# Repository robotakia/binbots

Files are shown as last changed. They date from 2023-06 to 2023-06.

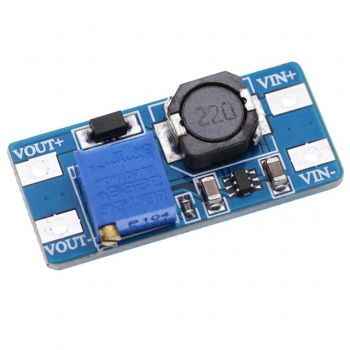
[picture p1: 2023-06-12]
Εξαρτήματα/Μετατροπέας DC-DC Step-Up 5-28V 2A - MT3608.jpg

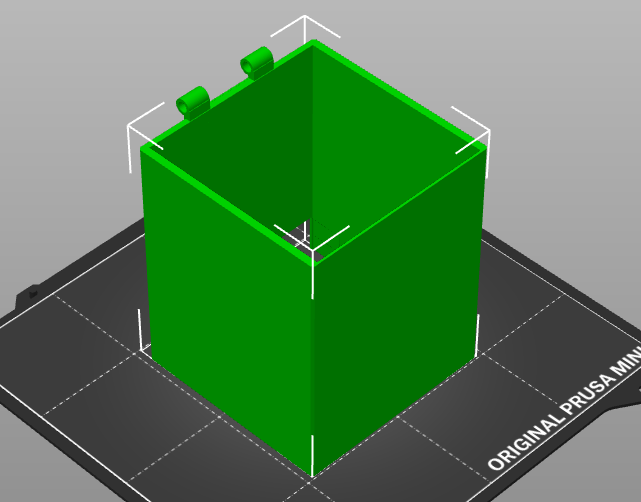
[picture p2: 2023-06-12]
3d printing/main_body.png

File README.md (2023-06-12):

Robotakia Binbots - Έξυπνο σύστημα διαχείρισης απορριμμάτων

5ος Πανελλήνιος Διαγωνισμός Ανοιχτών Τεχνολογιών στην Εκπαίδευση (2023)

Η ομάδα μας υλοποίησε μία μακέτα που αποτελείται από 2 έξυπνους κάδους ανακύκλωσης. Ο κάθε κάδος αντιστοιχεί σε ένα διαφορετικό ανακυκλώσιμο υλικό (π.χ. πλαστικό, χαρτί) και ενεργοποιείται αυτόματα μόλις κλείσει το καπάκι του. Στη συνέχεια ο κάθε κάδος ακολουθεί μία διαφορετική πορεία χωρίς καμία ανθρώπινη παρέμβαση ακολουθώντας τις αντίστοιχες χρωματιστές γραμμές. Επιπλέον, οι κάδοι αδειάζουν τα ανακυκλώσιμα υλικά σε διαφορετικά σημεία και με αυτόν τον τρόπο παρακάμπτεται το στάδιο της διαλογής των ανακυκλώσιμων υλικών.

Η ιστοσελίδα του έργου: https://openedtech.ellak.gr/robotics2023/robotakia-binbots/

Βίντεο παρουσίασης του έργου: https://youtu.be/iRQ4jEklhuc

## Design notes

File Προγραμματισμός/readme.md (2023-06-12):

Για τον προγραμματισμό του Pico με τη CirquitPython συνδέουμε το Pico με ένα καλώδιο usb στον υπολογιστή έχοντας πατημένο το κουμπί bootsel. Στη συνέχεια ρίχνουμε στον φάκελο του Pico το αρχείο adafruit-circuitpython-raspberry_pi_pico-en_US-8.0.5.uf2 . Ο φάκελος lib περιλαμβάνει τις απαραίτητες βιβλιοθήκες. Ο κώδικας που εκτελούν τα ρομποτάκια είναι τα αρχεία blue_bin.py και red_bin.py .

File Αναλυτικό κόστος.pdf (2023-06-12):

Εξάρτημα | Κόστος
Ball Caster with Metal Ball 0.4 | 1,2
Battery Holder 1x18650 with Wires | 0,6
Battery Lithium 18650 3.6V 3200mAh | 4,64
2 x DC Motor in Micro Servo Body | 5
Motor Drive Module Mini L298N | 2
Ks0021 keyestudio Collision Sensor | 3
Raspberry Pi Pico | 5,8
RGB Color Sensor with IR filter - TCS34725 | 9,9
Toggle Switch SPDT ON-OFF-ON (3A/250V) | 0,8
2 x Wheel 40x4mm (Hole Diameter 2mm) | 0,8
Μετατροπέας DC-DC Step-Up 5-28V 2A - MT3608 | 1,6
Σύνολο | 35,34

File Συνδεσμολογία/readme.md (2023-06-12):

Η συνδεσμολογία των ηλεκτρονικών εξαρτημάτων των ρομπότ.

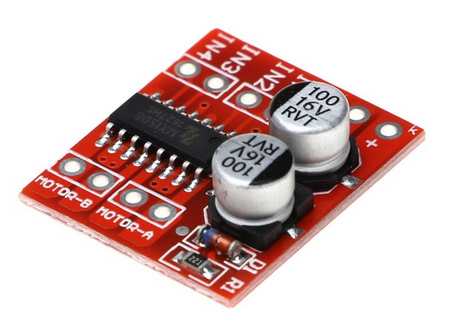
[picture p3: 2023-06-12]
Εξαρτήματα/Motor Drive Module Mini L298N.png

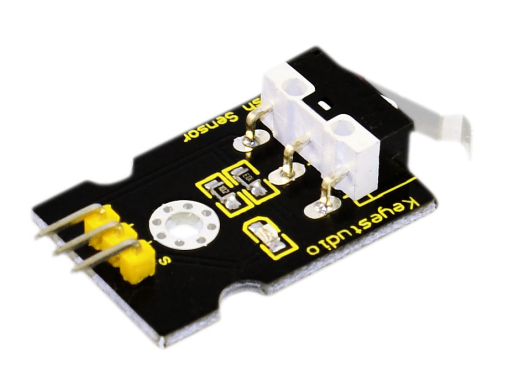
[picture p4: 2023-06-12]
Εξαρτήματα/Ks0021 keyestudio Collision Sensor.png

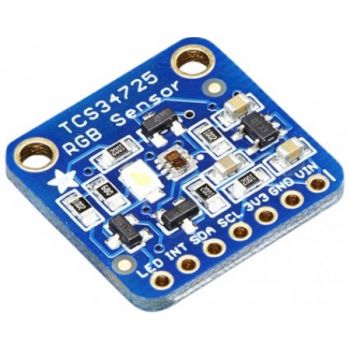
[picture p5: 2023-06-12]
Εξαρτήματα/RGB Color Sensor with IR filter - TCS34725.jpg

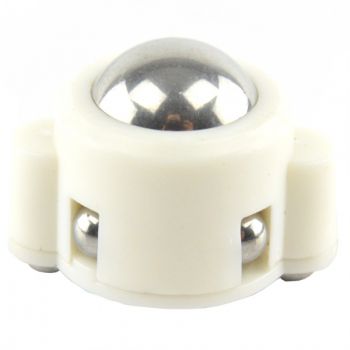
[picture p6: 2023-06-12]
Εξαρτήματα/Ball Caster with Metal Ball 0.4.jpg

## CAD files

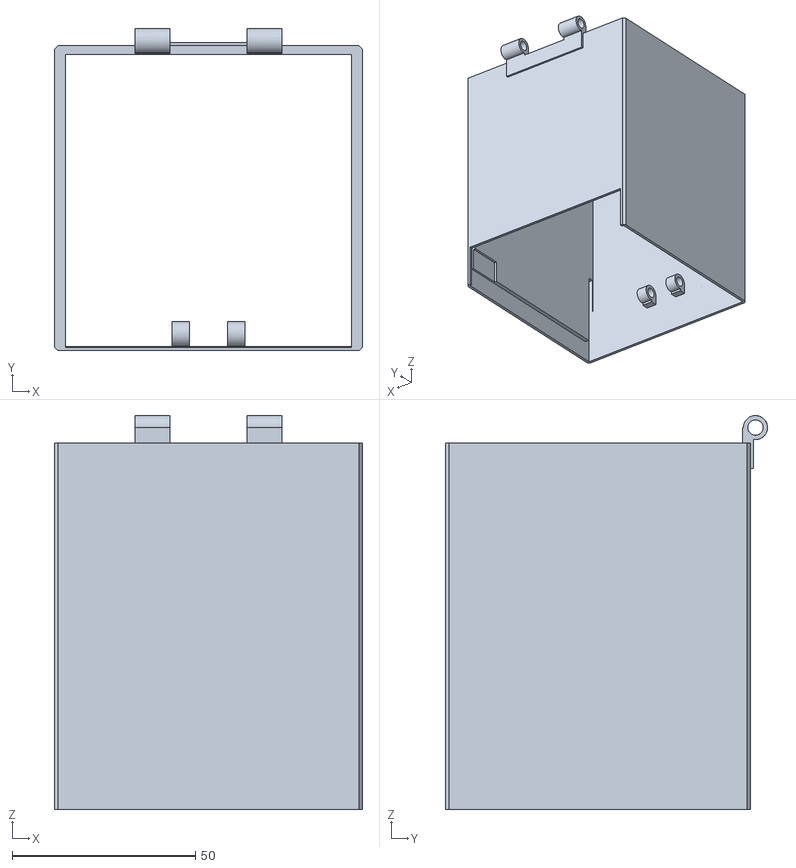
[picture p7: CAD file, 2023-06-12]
3d printing/main_body.stl
84.1 x 87.9 x 107.5

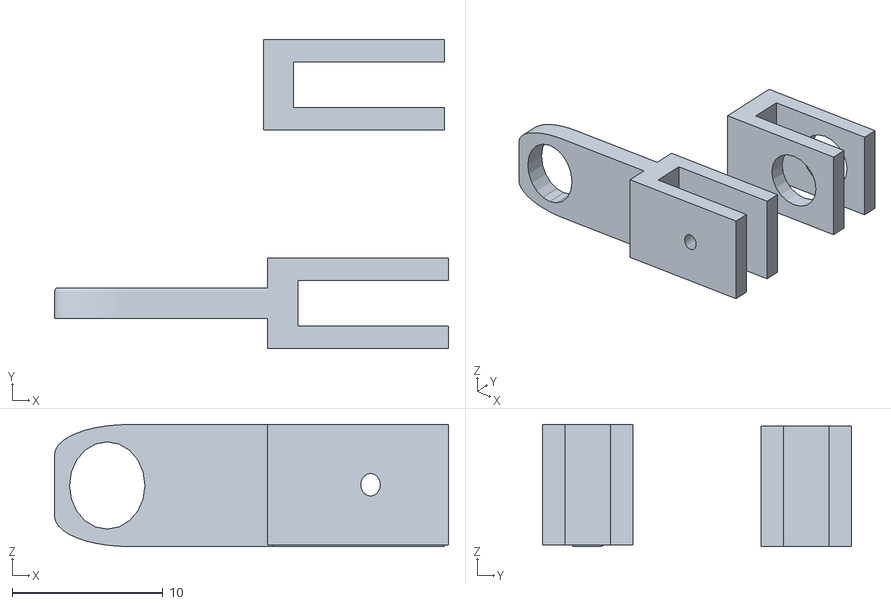
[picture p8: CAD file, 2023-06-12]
3d printing/piston.stl
26.2 x 20.5 x 8.10

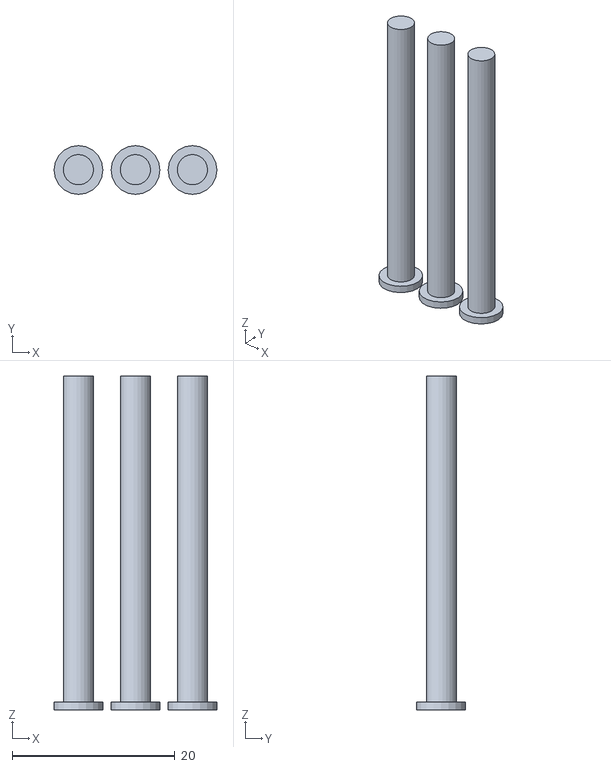
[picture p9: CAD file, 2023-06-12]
3d printing/pin.stl
20.0 x 6.00 x 41.0

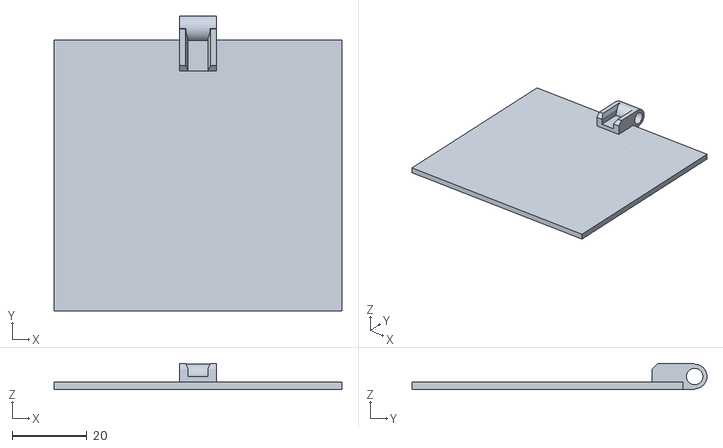
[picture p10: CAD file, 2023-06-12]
3d printing/inside.stl
77.0 x 79.0 x 7.00

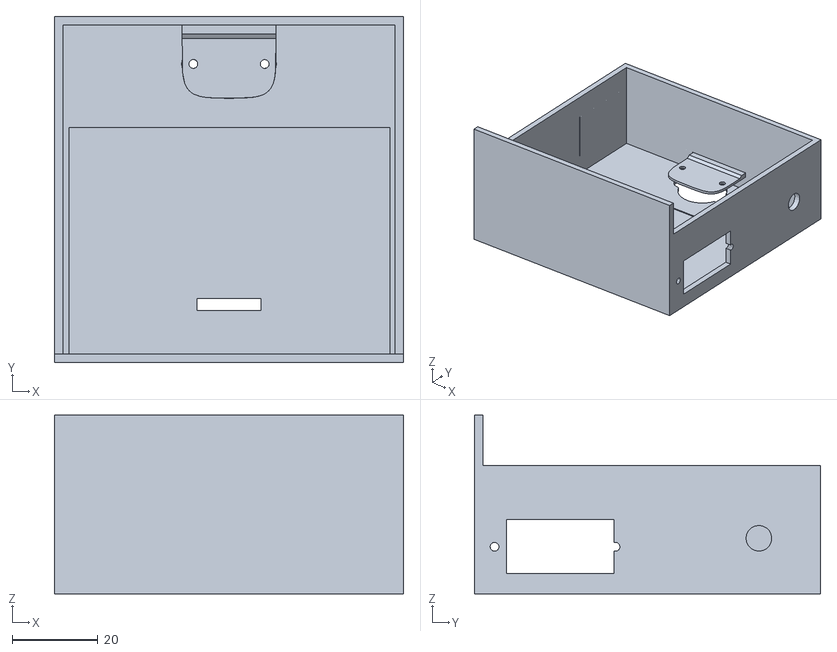
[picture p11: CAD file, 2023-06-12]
3d printing/bottom.stl
81.6 x 80.8 x 41.8

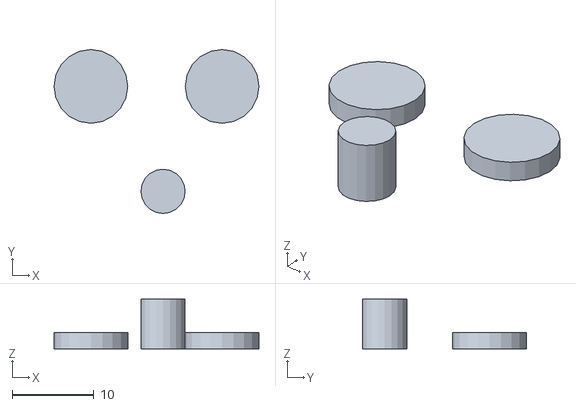
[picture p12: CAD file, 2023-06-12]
3d printing/axle.stl
25.0 x 20.0 x 6.05

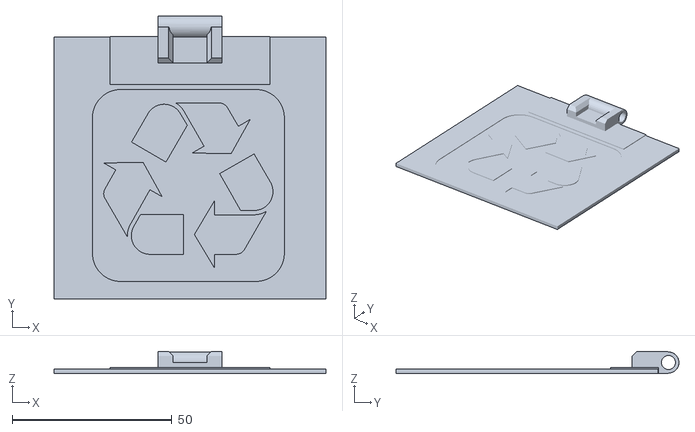
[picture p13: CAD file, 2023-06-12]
3d printing/top.stl
85.0 x 88.5 x 7.00

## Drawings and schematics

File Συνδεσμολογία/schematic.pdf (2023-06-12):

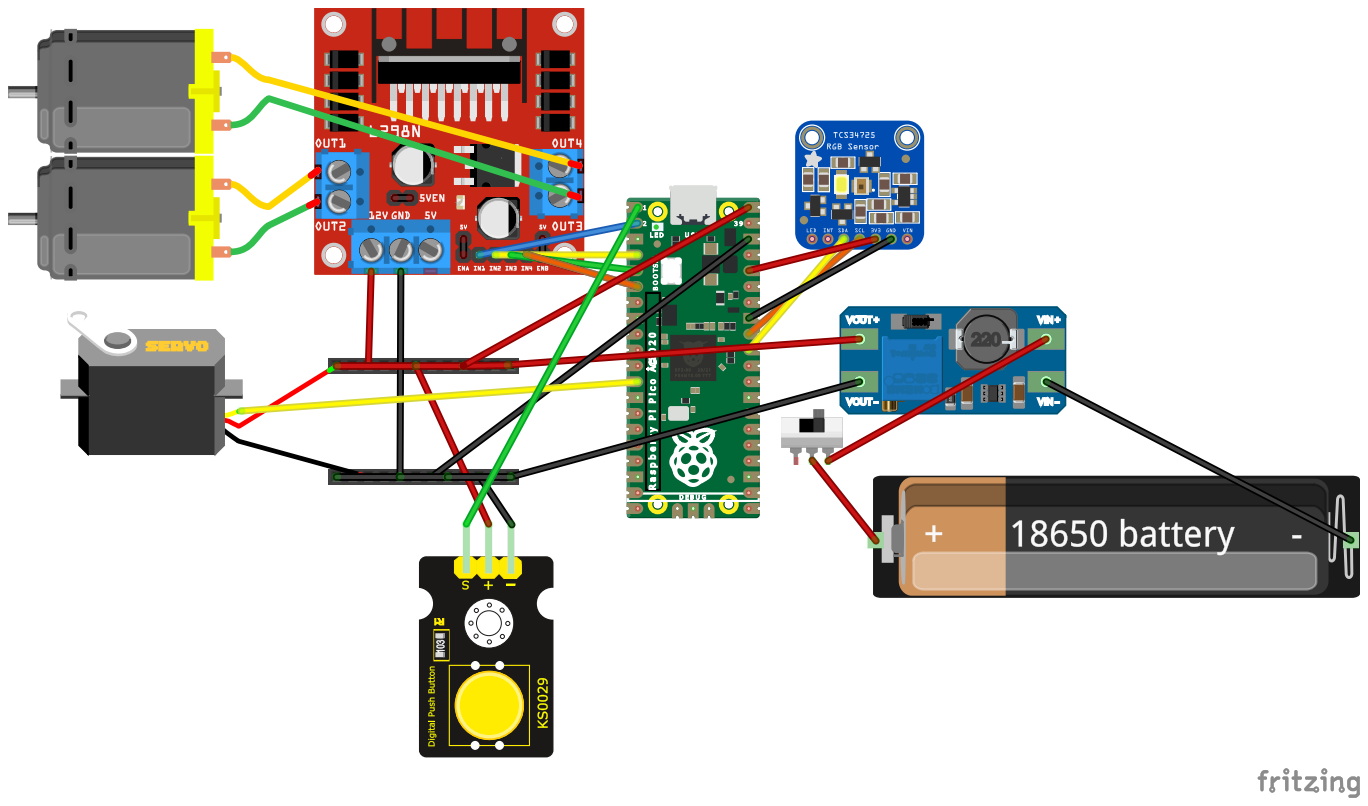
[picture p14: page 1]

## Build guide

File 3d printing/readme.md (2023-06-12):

Όλα αρχεία με τα μέρη των ρομπότ που τυπώνονται στον 3d printer.

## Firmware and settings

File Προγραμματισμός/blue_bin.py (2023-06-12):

import board
import digitalio
import pwmio
import busio
import adafruit_tcs34725
from adafruit_motor import servo
from time import sleep

i2c = busio.I2C(board.GP27, board.GP26)  # SCL-SDA
colorSensor = adafruit_tcs34725.TCS34725(i2c)

in1 = pwmio.PWMOut(board.GP1, frequency=1000)
in2 = pwmio.PWMOut(board.GP2, frequency=1000)
in3 = pwmio.PWMOut(board.GP3, frequency=1000)
in4 = pwmio.PWMOut(board.GP4, frequency=1000)

pwmServo = pwmio.PWMOut(board.GP9, duty_cycle=2 ** 15, frequency=50)
servo1 = servo.Servo(pwmServo, min_pulse=500, max_pulse=2200)

button = digitalio.DigitalInOut(board.GP0)
button.direction = digitalio.Direction.INPUT

def defineColor():
    global red, green, blue, yellow, black, white
    
    color_rgb = colorSensor.color_rgb_bytes
    temp = colorSensor.color_temperature
    lux = colorSensor.lux

    if color_rgb[0] > 70 and temp < 3000:
        red = True
        green = False
        blue = False
        yellow = False
        black = False
        white = False
        print('Red')
    elif color_rgb[1] > 30 and temp > 5000:
        red = False
        green = True
        blue = False
        yellow = False
        black = False
        white = False
        print('Green')
    elif color_rgb[2] > 30  and temp > 12000:
        red = False
        green = False
        blue = True
        yellow = False
        black = False
        white = False
        print('Blue')
    elif color_rgb[2] < 10 and lux > 9000:
        red = False
        green = False
        blue = False
        yellow = True
        black = False
        white = False
        print('Yellow')
    elif color_rgb[2] < 30 and lux < 2000:
        red = False
        green = False
        blue = False
        yellow = False
        black = True
        white = False
        print('Black')
    else:
        red = False
        green = False
        blue = False
        yellow = False
        black = False
        white = True
        print('White')

def speedConvertion(pin, speed):
    if speed < 0:
        speed = -speed
    duty = (65535*speed)/100
    duty = int(duty)
    if duty > 65535:
        duty = 65535
    pin.duty_cycle = duty

def move(leftSpeed, rightSpeed):
    if leftSpeed > 0:
        speedConvertion(in1, 0)
        speedConvertion(in2, leftSpeed)
    elif leftSpeed < 0:
        speedConvertion(in1, leftSpeed)
        speedConvertion(in2, 0)
    else:
        speedConvertion(in1, 0)
        speedConvertion(in2, 0)

    if rightSpeed > 0:
        speedConvertion(in3, 0)
        speedConvertion(in4, rightSpeed)
    elif rightSpeed < 0:
        speedConvertion(in3, rightSpeed)
        speedConvertion(in4, 0)
    else:
        speedConvertion(in3, 0)
        speedConvertion(in4, 0)

def UTurn():    
    move(20, -20)
    sleep(1.2)
    while not blue:
        move(20, -20)
        defineColor()
    move(0, 0)
        
def activateServo(start, stop, step):
    for angle in range(start, stop, step):
        servo1.angle = angle
        sleep(0.01)

def shake():
    for i in range(10):
        move(60, -60)
        sleep(0.1)
        move(-60, 60)
        sleep(0.1)
    move(0, 0)

def emptyTrash():
    UTurn()
    activateServo(80, 170, 1)
    shake()
    activateServo(170, 80, -1)

red = False
green = False
blue = False
yellow = False
black = False
white = False

activateServo(170, 80, -1)

while True:
    defineColor()

    if blue or black:
        move(0, 20)
    elif white or red:
        move(20, 0)
    elif green:
        move(0, 0)
        sleep(0.5)
        emptyTrash()
    elif yellow:
        while button.value == True:
            move(0, 0)
            sleep(0.01)
        UTurn()
    else:
        move(0, 0)
